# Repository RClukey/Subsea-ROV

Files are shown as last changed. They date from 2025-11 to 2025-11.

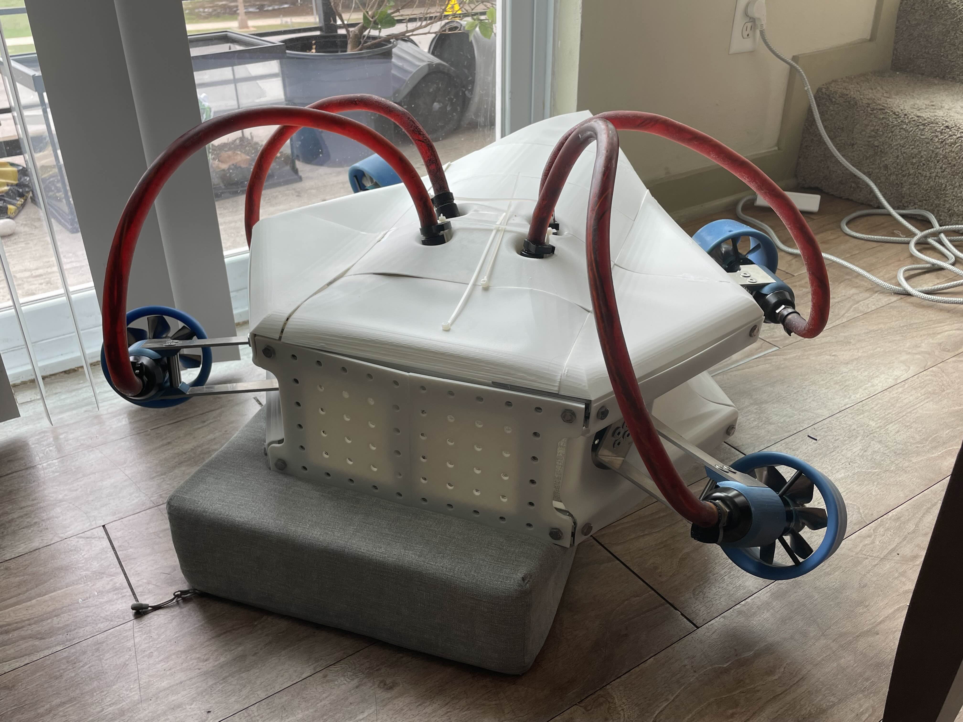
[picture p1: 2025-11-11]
Images-Videos/ROV Model Left.jpg

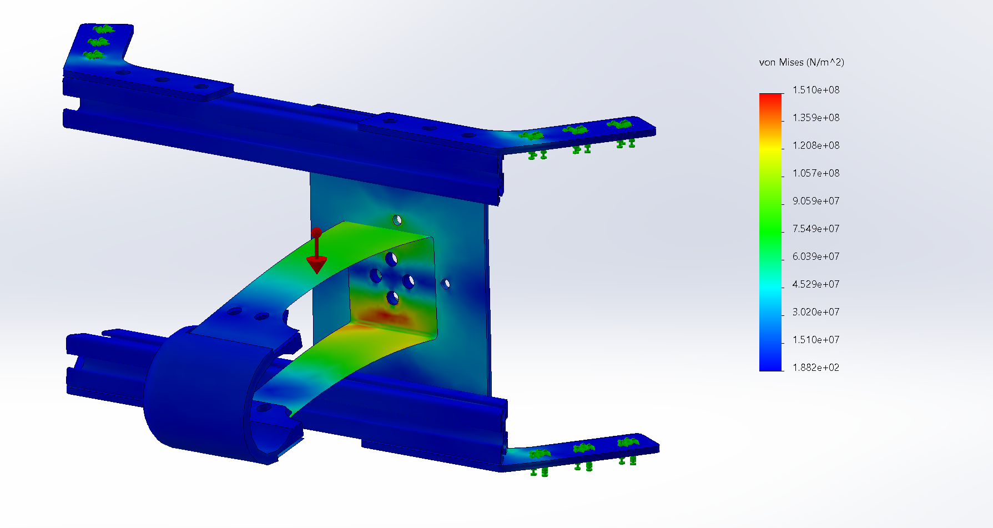
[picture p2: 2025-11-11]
Images-Videos/ROV Force Impact Simulation.png

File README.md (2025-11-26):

# Subsea Remotely Operated Vehicle (ROV)

During my robotics capstone at Texas A&M, my team and I were tasked to develop a subsea remotely operated vehicle (ROV). I led the CAD design and simulation work using SolidWorks, using the equations tool in SolidWorks to rapidly redesign the product based on the evolving client specifications. Each iteration of the design was simulated using SolidWorks' finite element analysis and hydrodynamics simulations to test the model's structural integrity and performance underwater. Once the core of the ROV's design was finalized, the team transitioned to fabricating the prototype to physically simulate the design in the real world. Even then, we continued making daily adjustments to the design improving strength, buoyancy, and hydrodynamics, which meant the physical model had to be altered to match the newer SolidWorks designs. Working in that rapidly iterative environment — constantly shifting between digital modeling and hands-on validation — taught me how to move quickly, troubleshoot effectively, and stay adaptable to the specifications of the design.

The CAD Models repository includes all the CAD models that were used to create the design for the ROV structure and propulsion system.

The Images-Videos repository includes a lot of the pictures and videos throughout the project.

SubseaROV_DOF-Animation.gif shows the CAD design and range of motion of the thrusters for the subsea ROV. Each thruster has independent rotation controls and thrust controls allowing for full 6 degrees of freedom.

SubseaROV_Mid-Report.pdf shows the mid-semester report for our capstone team, after the design was determined, but before the design was fabricated.

SubseaROV_Final-Report.pdf shows the end of semester report for our capstone team, after the design was fabricated and tested.

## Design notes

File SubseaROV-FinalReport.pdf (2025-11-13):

## Final Design Report Next-Generation Subsea ROV

## Prepared For: Mr. William Ledbetter Mr. Don Wells

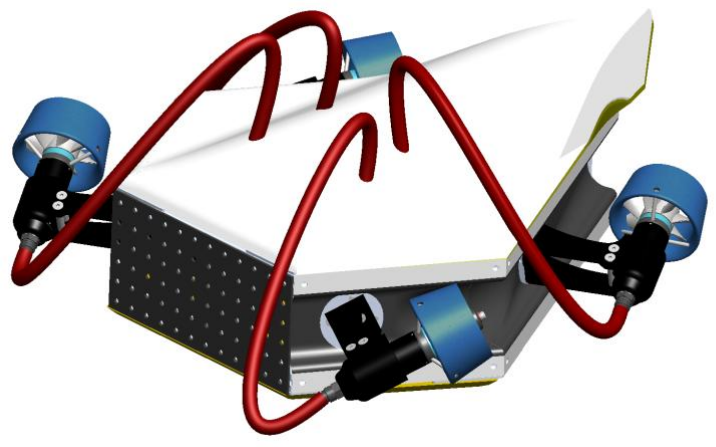
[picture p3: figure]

## Presented to Dr. Andrew Conkey

## Prepared by: Ocean Gig Eric Bauman Bobby Clukey Heath Garrett Marcus Navas David Scott

## Texas A&M University Department of Multidisciplinary Engineering ITDE 402 – Spring 2025 – Sections 501/M01

## April 21, 2025

Texas A&M University-MTDE-Final Report. – Ocean Gig | 2

Executive Summary
Next-Generation Subsea ROV

When divers operate underwater, they encounter numerous hazards inherent to the environment. To reduce these risks, underwater remotely operated vehicles (ROVs) have been developed to minimize the need for direct human involvement in dangerous conditions. However, current ROVs lack the ability to move and perceive their surroundings with the same flexibility and precision as a human diver. The objective of this project was to develop an ROV capable of replicating diver-like movement and performing tasks typically executed by divers. The specific focus for this team was the design and construction of the chassis and propulsion systems.

At the start of the semester, preliminary progress had been made in computer-aided design (CAD), and many analytical aspects of the project had been outlined. However, all work up to that point remained theoretical, with no physical components assembled. The only available hardware consisted of thrusters that had been generously donated, as well as the electronics to power these thrusters.

This report presents the analytical diagrams and charts used to identify critical needs, functions, and design solutions that contributed to the development of the final product. It also includes financial documentation to confirm the project remained within budget, along with a detailed overview of the ROV’s construction process.

The completed project resulted in a fully built ROV chassis with thrusters capable of providing six degrees of freedom. This configuration enables the ROV to maneuver through water in a manner that closely simulates the movements of a human diver. With this completed model, the team was able to test the 6-degrees of freedom of the ROV, the strength of the ROV, and attempted to test the force output of the thrusters given different power inputs.

Special recognition is extended to Professor William Ledbetter and Mr. Don Wells for their generous support throughout the project, and to Dr. Andrew Conkey and Professor Oscar Lopez for their assistance throughout the capstone project. Appreciation is also given to members of Oceaneering International, Inc. for their valuable insights and willingness to share their expertise in subsea ROV technology.

Texas A&M University-MTDE-Final Report. – Ocean Gig | 3

Demonstration of ABET Student Outcomes and Performance Indicators

Student Outcome (SO) | Performance Indicator (PI) | Page Numbers in this Report Showing Demonstration of this SO/PI
SO 1: An ability to identify, formulate, and solve complex engineering problems by applying principles of engineering, science, and mathematics | 1-A. An ability to identify complex engineering problems and initiate problem-solution processes | Pages 7-13
| 1-B. An ability to carry out an engineering problem solution process to completion | Pages 24-28
| 1-C. An ability to apply fundamental principles of engineering, science, and mathematics in an engineering problem-solution process | Pages 22-23 Pages 30-32
SO 2: An ability to apply engineering design to produce solutions that meet specified needs with consideration of public health, safety, and welfare, as well as global, cultural, social, environmental, and economic factors | 2-A. An ability to determine needs to be satisfied by an engineered solution and interpret and consider needs in contexts of health, safety, welfare, global, cultural, social, environmental, and/or economic contexts, as appropriate. | Pages 33-35
| 2-B. An ability to implement a logical, orderly, and documented design process driven by defined needs. | Pages 14-21
SO 5: An ability to function effectively and professionally on a team whose members together provide leadership, create a collaborative and inclusive environment, establish goals, plan tasks, and meet objectives | 5-A. An ability to function effectively on a team by contributing to the team effort through collaboration and the creation of a collaborative and inclusive environment. | Pages 38-40
| 5-B. An ability to function effectively on a team by exercising appropriate leadership to establish goals, plan tasks, and meet objectives. | Pages 7-8 Pages 38-40
SO 6: An ability to develop and conduct appropriate experimentation, analyze and interpret data, and use engineering judgment to draw conclusions and propose recommendations | 6-A. An ability to develop and conduct experiments appropriate for engineering applications. | Pages 22-23 Pages 30-32
| 6-B. An ability to analyze and interpret experimentally derived data. | Pages 22-23 Pages 30-32
| 6-C. An ability to use appropriate engineering judgment with analysis of experiments to formulate conclusions and propose recommendations. | Pages 22-23 Pages 30-34

Texas A&M University-MTDE-Final Report. – Ocean Gig | 4

## Final Design Report

Next-Generation Subsea ROV

### Table of Contents

EXECUTIVE SUMMARY | 2
DEMONSTRATION OF ABET STUDENT OUTCOMES AND PERFORMANCE INDICATORS | 3
List of Figures and Tables | 5
Glossary/Nomenclature | 6
INTRODUCTION | 1
Project Recap | 1
Concept Overview | 3
Initial Concept | 3
Modified Concept | 5
DETAILED DESIGN OVERALL SYSTEM | 8
Functional Diagrams | 8
Functional Analysis Diagrams (FAD)/Functional Flow Diagram (FFD) | 8
Physical Layout Diagrams | 9
Geometric Layout | 11
Bill of Materials | 13
Estimated Cost for Prototype | 15
DETAILED DESIGN: ENGINEERING ANALYSIS | 16
“THE BUILD” -FABRICATION/CONSTRUCTION/PRODUCTION/SYNTHESIS/CODING | 18
Stage 1: Frame Construction | 18
Stage 2: Thruster Arm Construction | 19
Stage 3: Skin Construction | 21
Stage 4: Electrical Connection | 23
Testing/Verifying/Validating/Experimental Plan | 24
Safety/Hazard Assessment and Evaluation | 27
RELIABILITY ASSESSMENT | 28
SOCIETAL FACTORS AND IMPACT | 29
FUTURE WORK | 30
TEAM AND PROJECT ORGANIZATION, PLANNING, AND EXECUTION | 32
SUMMARY | 35
Appendix | 36
A. List of Abbreviations and Terminology | 36
B. References | 36
C. Order of Magnitude and Detailed Calculations | 37
E. Detailed working drawings/models/assembly | 38
F. Testing/Validating/Verification/Experimentation | 39

### List of Figures and Tables

Figure 1. Chassis Subsystem House of Quality (team-fig) - 1 Figure 2. Propulsion Subsystem House of Quality (team-fig) - 2 Figure 3. Isometric drawing of The Turkey design. (team-fig) - 3
Figure 4. The final fall semester CAD drawing (team-fig) - 4
Figure 5. The mid-semester model of the ROV (team-fig) - 6
Figure 6. The final design of the ROV without the syntactic foam (team-fig) - 7 Figure 7. The final design of the ROV with the syntactic foam (team-fig) - 7
Figure 8. Functional Analysis Diagram for the subsea ROV. (team-fig) - 9
Figure 9. Physical layout of the chassis and propulsion subsystems (team-fig) - 10
Figure 10. Wiring diagram for the thruster power and control system provided by Tecnadyne. (Tecnadyne)
- 10
Figure 11. Internal view of the ROV showing the electronics, syntactic foam, frame, rotary actuators, and thruster. (team-fig) - 11
Figure 12. Exploded view of the ROV showing the key components of this phase of the design project. (team-fig) - 12
Figure 13. Calculations of Archimedes’ Principle in SolidWorks. (team-fig) - 16
Figure 14. A team member cuts an aluminum bar using an FEDC chop saw. (team-fig) - 18
Figure 15. The completed aluminum frame of the chassis. (team-fig) - 19
Figure 16. A team member prepares to bend the aluminum section of the thruster arms. (team-fig) -20 Figure 17. A thruster sitting in the thruster clamp and aluminum arm. (team-fig) - 20
Figure 18. Top skin panel with space for the clips on the thruster tubing. (team-fig) - 21
Figure 19. Port isometric view of the ROV with the skin panels (team-fig) - 22
Figure 20. Starboard isometric view of the ROV with the skin panels (team-fig) - 22
Figure 21. The wiring for the power subsystem is connected to the subsea thruster. (team-fig) - 23 Figure 22. Stress/strain curve for 5052 Aluminum (team-fig) - 24
Figure 23. Stress heat map for a 50-pound force acting on the thruster clamp acting downward with the thruster arm horizontal (team-fig) - 25
Figure 24. Stress heat map for a 90-pound force acting on the thruster clamp acting downward with the thruster arm vertical (team-fig) - 26
Figure 25. The WBS for the design and manufacturing process. (team-fig) - 33
Figure 26. The projected Gantt chart for the semester. (team-fig) - 33
Figure 27. The actual completion times for tasks are between March and April. (team-fig) - 34

Figure C.1. Calculations of Archimedes’ Principle in SolidWorks. (team-fig) - 37
Figure C.2. Excel representation of the resultant force and torque vectors given thruster positions and output forces. (team-fig) - 37
Figure E.1. Enlarged model of the wiring diagram for the thruster power and control system - 38 Figure F.1. Enlarged representation of the resultant force and torque vectors given thruster positions and output forces. (team-fig) - 39

Table 1. SWOT Analysis for the ROV (team-fig) - 5
Table 2. Bill of materials for the prototype (team-fig) - 13-14
Table 3. Cost estimate table for the project (team-fig) - 15
Table 4. Future work areas that will be covered in coming years (team-fig) - 30-31

Texas A&M University-MTDE-Final Report. – Ocean Gig | 6

### Glossary/Nomenclature

- CNC: Computer Numerical Control
- DOF: Degrees Of Freedom
- FAD: Function analysis diagram
- Full Depth Rated: Rated to withstand the pressures at the bottom of the Marianas Trench, the deepest part of the ocean.
- Propwash: The effect that thrusters have on the fluids passing through them. This effect makes the fluids rotate in a spiral pattern after passing through the propeller.
- ROV: Remotely Operated Vehicle
- SWOT: Strengths, Weaknesses, Opportunities, and Threats
- Tether (Umbilical): The wired connection between the ROV and the pilot on the surface which powers the ROV and controls the thruster directions and powers.
- WBS: Work Breakdown Structure

Detailed Design Report-FR– | Spring 2025

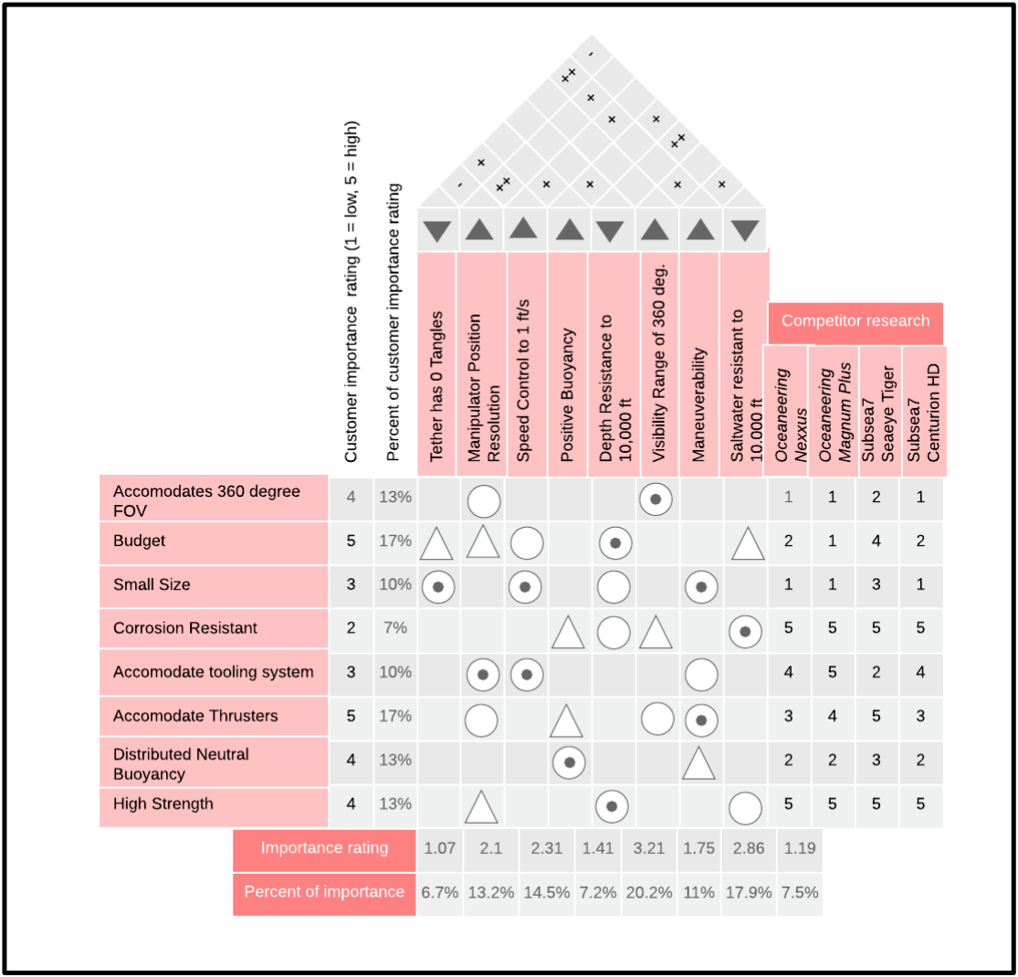
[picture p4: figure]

Texas A&M University MTDE– Ocean Gig | Page 1

Introduction

Project Recap
The goal of this project is to create a Subsea ROV that possesses the ability to move and see like a human diver. This constitutes characteristics such as the ROV having 6 degrees of freedom, access to 360 degrees of visibility, and having a borescope to be able to look around objects the way a human head/neck combination provides. From the QFDs (Figures 1 and 2 ), the team determined the top-level measures that produce a successful project, including keeping the overall cost of the ROV minimal within the team's budget and keeping the maneuverability of the ROV ahead of the current industry leaders in subsea ROV about tether accommodation and thruster capability.

Figure 1. Chassis Subsystem House of Quality (team-fig)

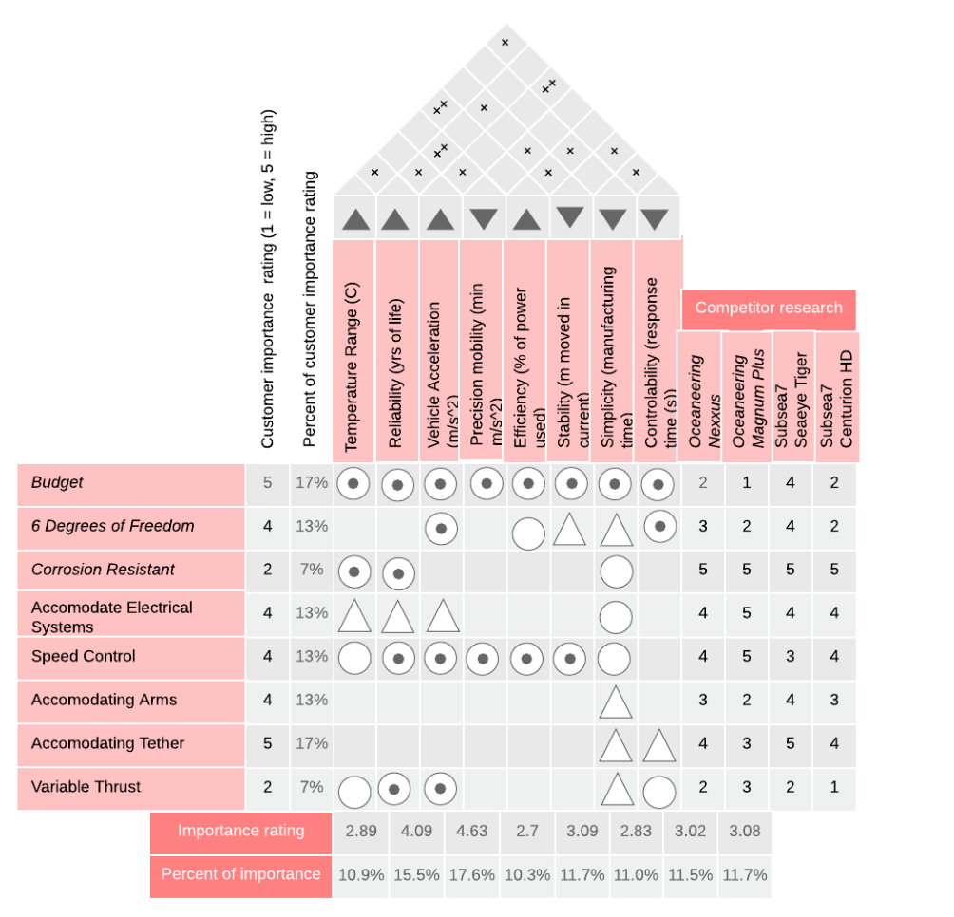
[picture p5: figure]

Figure 2. Propulsion Subsystem House of Quality (team-fig)

As the design progressed, the focus shifted to the more fundamental deliverables. A well-designed frame that provided efficient use of space to accommodate electronics, a buoyancy system, and the rotating thrusters were paramount. We also put a deeper focus on completing the mounting of the thrusters to be able to represent our proof of concept within the time frame we were working within. We kept the needs of the QFD in mind by prioritizing the design of the frame conscious of buoyancy, as that is the determining factor in an ROV that functions under the water, as well as making sure the thrusters can provide the control that is key to our project.

Concept Overview
This section of the report covers the development of the initial solution to the need statement and how that concept evolved to the final design the team worked towards.

Initial Concept

At the beginning of the semester, the dimensions of the frame had been essentially finalized, having decided on an optimum shape. The mounting location of the thrusters and rotary actuators was also known. The rotary actuators would not be implemented into the final design due to the heavy power needs, weight, and expensive cost. The skin panel shapes were also roughly determined based on the desire to create a hydrodynamic shape that provided strength as well as thruster, tether, manipulator, and camera accommodation.

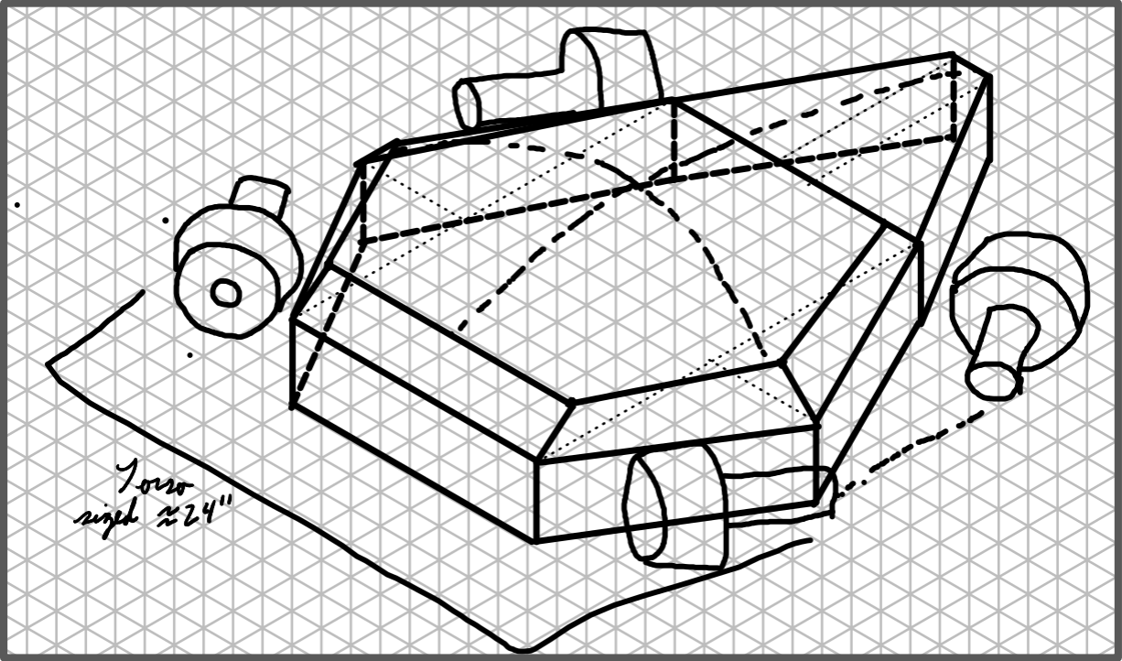
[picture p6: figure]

Figure 3. Isometric drawing of The Turkey design. The design was planned to be 24 inches long, 25 inches wide, and 10 inches tall. These dimensions are consistent with the prototype. (team-fig)

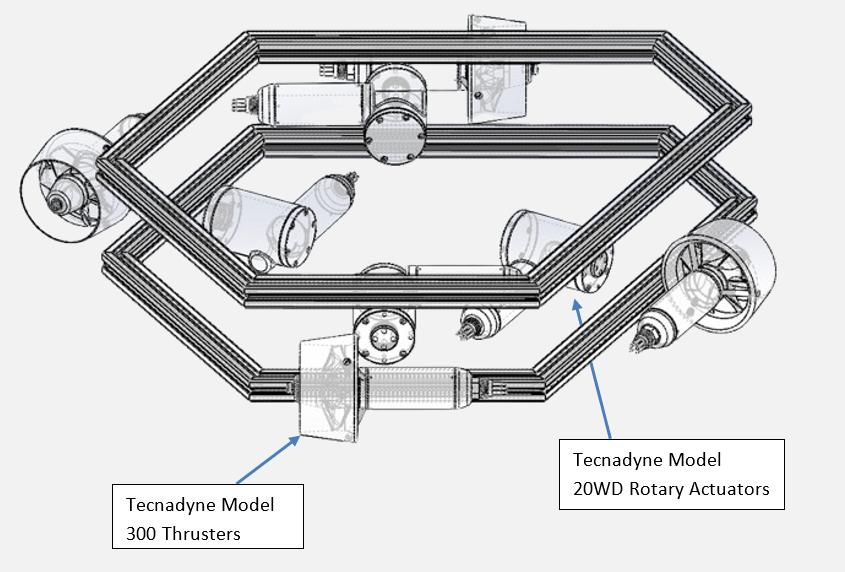
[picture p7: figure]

Figure 4. The final fall semester CAD drawing with the Tecnadyne Model 300 thrusters and Tecnadyne Model 20WD rotary actuators labeled. (team-fig)

Most of the strengths of the ROV project came from this being a multi-year project. As this was the third year of a five-year project, the team had two years of work to build upon. One of the strengths that didn’t come from the length of the project was the modularity and scalability of the design of the ROV. If the dimensions of the beams and the power of the thrusters were to be increased, the capabilities of the ROV, such as the payload and depth resistance, could also be increased.

The weaknesses of this project stemmed from the lack of experience the team had with certain parts of the project’s scope. Part of our work was to create the power system for the ROV. None of the team members in the project were power engineers, and as such, no one had experience working with the power system. Another weakness came from the project’s budget. The rotary actuators the team was going to use cost $12,000 each. This means the 4 rotary actuators that had originally been planned for would go well over the budget of $10,000.

The opportunities that this project has given the team come from the design of the ROV and the industry leaders who have been able to help with the creation of the ROV. The 6 degrees of freedom on the ROV provide multi-directional capabilities that mimic a diver’s motions. The team also worked with Oceaneering and The Subsea Tieback Foundation to determine how the current industry creates subsea ROVs and where the current solutions could be improved upon to create the next-gen ROV design.

The threats to the ROV project, much like the weaknesses, came from the lack of knowledge in power engineering. None of the team members were power engineers, and as such, the team needed to learn how to deliver the necessary power to the thrusters, rotary actuators, cameras, and manipulators for the ROV to function like a human diver. Another threat to the project, which can be a major problem in future stages of the project, is that the team’s sponsors specifically stated that marinization should not be a priority. This could affect how much of the team's work will be useful to the future years of the project. Something the team might have thought was important to design the ROV around might not be marinized, and as such would have to be replaced, thus changing the design of the project.

Table 1. SWOT Analysis for the ROV (team-fig)

Strengths: ● Concept ● Industry connections through sponsors ● Static Mechanical analysis ● Access to previously acquired parts ● Access to previous work done ● Modularity and scalability of design | Weakness: ● Undeveloped power system ● Lack of full CAD model ● Vagueness of certain specifications ● Lack of access to CAD models for electrical components ● Potential costs ● Fluid analysis ● Limited testing environment
Opportunities: ● Advanced Maneuverability ● Size-accommodated exploration possibility ● Innovation in overall geometry ● Creation of a next-gen ROV that mimics the motions of a human diver ● Modularity and scalability of design ● 6 degrees of freedom | Threats/Risks: ● Needing expensive parts and possibly going over budget for specific pieces of equipment ● Understanding of circuitry for power systems ● Our part of the project is not concerned with marinization, which could cause compatibility issues further down the road ● Combining previous groups' work into our frame

Modified Concept

The main shape of the ROV remained constant throughout the semester, however the externals of the ROV went through various changes to best shape for hydrodynamics, buoyancy, and overall ROV strength.

In the beginning of the semester, there was only the frame, thrusters, and rotary actuators in the ROV model. The dry weight for this version of the ROV was 46.2 pounds, while the wet weight was 32 pounds.

The first modification to the design of the ROV included adding the syntactic foam used for floatation and close to neutral buoyancy and the electronics that would power the thrusters. However, no skin was included to protect the internals of the ROV. The majority of the syntactic foam was positioned above the ROV to raise the center of buoyancy, the geometric center of the ROV, above the center of mass. This will allow the ROV to orient itself right-side up. The closer the center of mass and center of buoyancy were together, the slower the ROV would self-orient, meaning less force would be required from the thrusters to maintain an angled position if the ROV requires an angle while in operation. The dry weight for this version of the ROV was 71 pounds, while the wet weight was 3.3 pounds. This was a significant improvement from the initial design of the ROV. The team chose not to aim for true neutral buoyancy, as the addition of the manipulator to the front of the ROV would affect the ROV’s center of mass and the overall buoyancy.

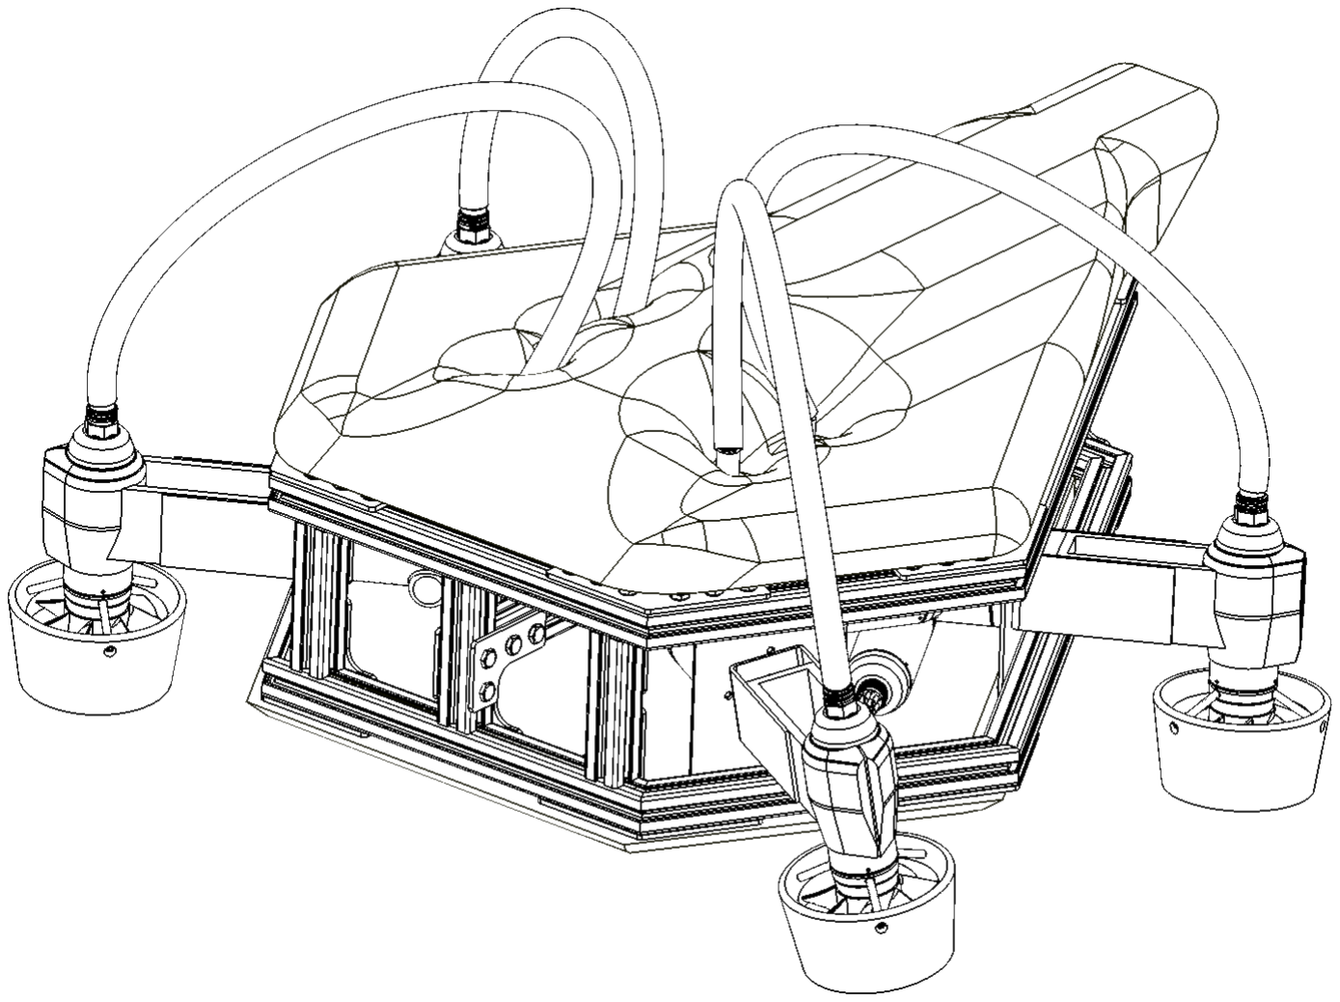
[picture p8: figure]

Figure 5. The mid-semester model of the ROV (team-fig)

The next and final improvement on the design came with the skin panels on the sides, top, and bottom. The skin panels protected the important electrical components inside the ROV and the syntactic foam from being damaged. The panels also prevented fish and other sea creatures from getting inside the ROV and affecting the operations of the ROV. The panels also provided a rigid body for water to flow around, instead of having the turbulent water from the thruster flow through the ROV, thus improving the hydrodynamics of the ROV. This design also came with a slight modification to the design of the syntactic foam because the introduction of the skin panels and an atmospheric pressurized vessel for the electronics affected the wet weight of the ROV. The dry weight for this final version of the ROV was 72.4 pounds, while the wet weight was 2.9 pounds. The skins on the side of the ROV allowed for optimal flow of water through the thrusters while decreasing the effects of propwash between the thrusters and providing protection to the electronics and syntactic foam to prevent damage.

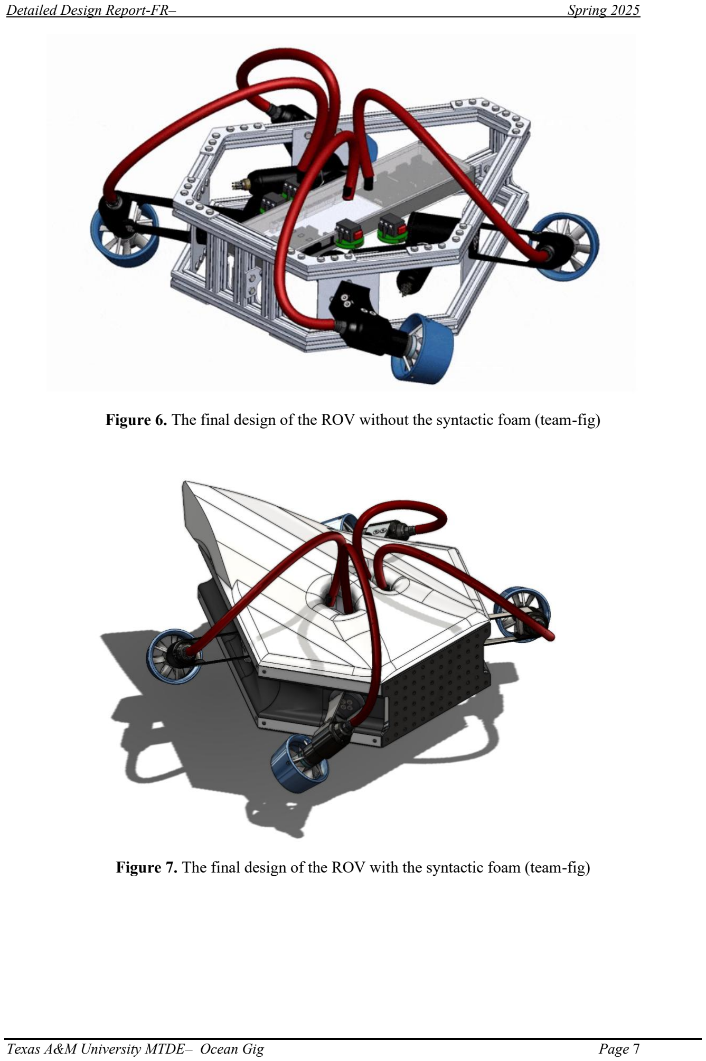
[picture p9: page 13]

Figure 6. The final design of the ROV without the syntactic foam (team-fig)

Figure 7. The final design of the ROV with the syntactic foam (team-fig)

Detailed Design Overall System
This section details the chain of interfacing design elements that will result in a product that completes defined function requirements. These tools lay out the path of travel from power and/or operator input to output by the design prototype. This is an opportune way to understand how the product was designed and what components are responsible for intermediate functions, multiple functions, and how key design requirements had to be revised since brainstorming and proof of concept. This is a relevant mindset for this project in particular as this stage of the ROV design contained chassis and propulsion system design aspects.

This next-generation ROV’s unique thruster capability and optimized shape is shown through detailed design diagrams to have important relationships, while still maintaining numerous independent design elements. For example, the functional flow diagram shows that the camera system will relay information through the electronics and allow the operator to take advantage of the more convenient chassis shape and thruster-provided degrees of freedom.

Functional Diagrams
These diagrams display the functional “path” of the design. Via the design requirements, projects are designed with the end operations in mind, and by understanding the components involved and how they interact with one another, a sort of roadmap can be created to flow through the interfaces from inputs to outputs, with outputs being the aforementioned design requirements. In the case of the ROV, this will mainly pertain to the mobility of the ROV being provided through the thrusters via electrical power, with the chassis holding everything steady.

Functional Analysis Diagrams (FAD)/Functional Flow Diagram (FFD)

The functional analysis diagram is the roadmap from operator inputs to ROV motion and vision. This diagram outlines the ROV’s design capabilities from the point that the operator inputs a command based on their senses via the cameras that will be integrated into the ROV. This operator input is transmitted to the ROV’s electronic systems via the tether. The electronic systems control the cameras, rotary actuators, manipulators, and thrusters, which will allow these subsystems to function as intended. The chassis provides structural support and protection for these components by being designed such that the frame takes the force of the impacts, and the skin prevents rocks and fish from damaging the electronics. The thrusters provide movement to the ROV via the propellers, however, the water can also move the ROV through currents that must be taken into account.

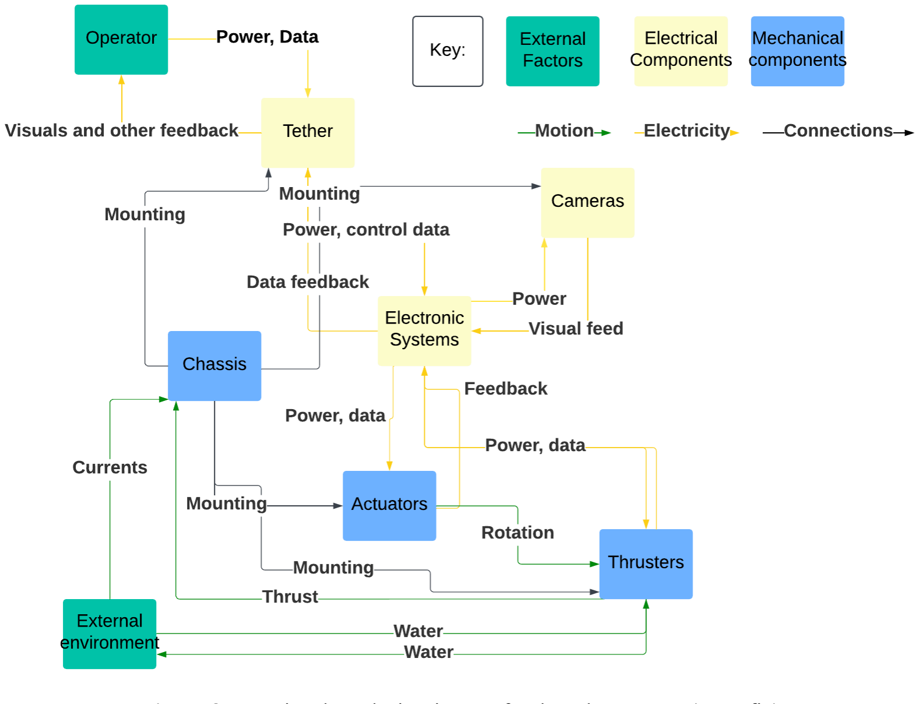
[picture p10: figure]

Figure 8. Functional Analysis Diagram for the subsea ROV. (team-fig)

Physical Layout Diagrams

Chassis and propulsion layout:

The chassis and propulsion layout is shown below in Figure 9 & 10. This shows the locations of the syntactic foam, electronics, frame, rotary actuators, thrusters, and skin about each other. The syntactic foam is on both the bottom and top to provide buoyancy to the ROV. The electronics are encased in an atmospheric pressure vessel full of air so the electronics can function underwater. The frame is constructed out of aluminum bars and sheet metal, and stainless steel bolts and fasteners. The rotary actuators and thrusters come from Tecnadyne, both of which are full-depth rated (11,000 meters). Lastly, the skin is made out of ABS plastic which would be vacuum-formed using molds to protect the ROV.

## Skin

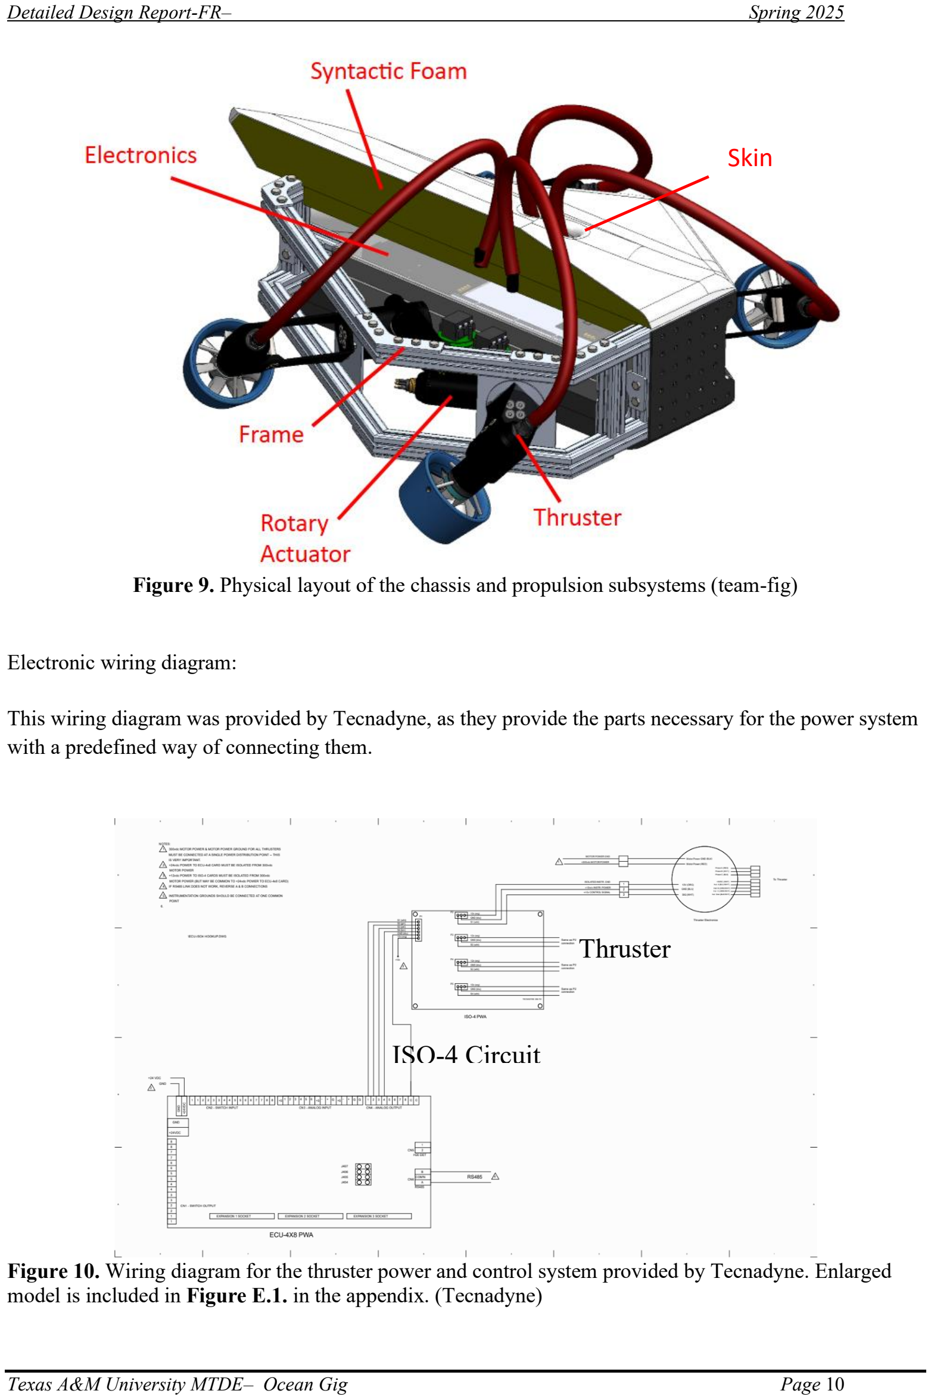
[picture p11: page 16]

Figure 9. Physical layout of the chassis and propulsion subsystems (team-fig)

Electronic wiring diagram:

This wiring diagram was provided by Tecnadyne, as they provide the parts necessary for the power system with a predefined way of connecting them.

Figure 10. Wiring diagram for the thruster power and control system provided by Tecnadyne. Enlarged model is included in Figure E.1. in the appendix. (Tecnadyne)

## Thruster

## ISO-4 Circuit

The power subsystem, excluding components that only are used to affect the control voltage, properly begins at the ISO-4 card and continues to the thruster electronics module and into the thruster itself (not shown).

The ISO-4 circuit boards take in a 12V DC instrumentation power signal and four +/- 5V control signals, and outputs four isolated sets of 12V instrumentation power and a +/- 5V control signal. These signals are what is passed into the thruster electronics module and from there into the thruster.

The thruster electronics module takes in the signals from the ISO-4 circuit board as well as a separate, isolated 300V power source, conditions these signals, and passes them to the thruster.

The separate circuit board that is not part of the power system is an ECU 4x8 BIOS, which takes in computer commands and outputs a corresponding control signal voltage between -5 and +5 volts.

Geometric Layout

The Subsea ROV capstone project for the 2024-2025 school year consisted of chassis and propulsion design engineering. The geometric layout will provide diagrams and point out the key components of said chassis and propulsion components that were designed to meet the client's specifications for the next-generation ROV design prompt. Provided are cutaway views as well as exploded models to better understand the ROV and the interfacing of the components, as this is a key part of the 2 overarching design areas. The chassis was designed with the intention of providing a diver-like shape that will be noticeable in use, but also to receive the thruster system that will constitute the execution of free movement in all 6 degrees of freedom as one would be capable of doing were they underwater.

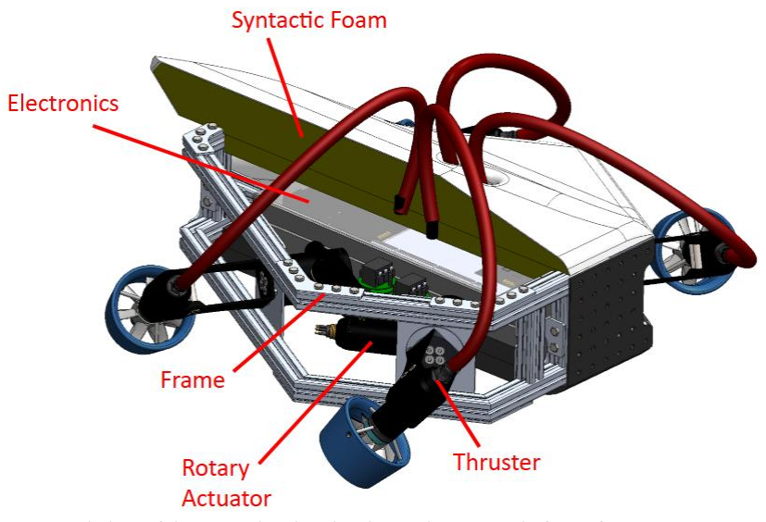
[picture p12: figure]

Figure 11. Internal view of the ROV showing the electronics, syntactic foam, frame, rotary actuators, and thruster. (team-fig)

Figure 12. Exploded view of the ROV showing the key components of this phase of the design project. (team-fig)

The ROV model displayed above is the final iteration of the design. The ability to see the final shape of the constructed prototype as well as the inside of the top and side skin panels connects the dots between the overall shape and components. The skin gives way to the frame, designed with the previous team’s coffin shape in mind but now optimized to provide structural rigidity and be easily scalable to accommodate the growing amount of centrally-placed electronic components that will power systems in the future. The frame is intended to provide a hydrodynamically advantageous shape of a human torso when submerged, emphasized by the smooth, curvaceous skin panels. The inside of the ROV is available to future teams for power components, control system electronics such as rotary actuators, and the syntactic foam that will be calibrated to provide near-neutral buoyancy. The thrusters are placed between the angled sections of the frame on the port and starboard faces. This placement is strategic to the 6 degree of freedom design goal. The free rotation that will be provided by the rotary actuators will allow for the thrusters’ angles of orientation to allow a force vector in any direction, allowing the operator to move freely without limitation or the necessity of calculating every adjustment based on the limited mobility of the ROV.

Bill of Materials

Table 2. Bill of materials for the prototype (team-fig)

Item No. | Sub System description | Part Specs | Description | Cost Per Unit | Quantity | Total Cost
1 | Extruded Aluminum Bars | 1”x3’, solid, smooth finish | Aluminum bars serve as light but rigid frame sections. Extruded quality will allow for effective component mounting and allow adjustments. | $15.90 | 7 | $110
2 | Sheet Aluminum 5052 | 1/8”, 24” x 24” | One sheet of specified grade aluminum; is used to supply frame connecting brackets, as well as thruster mounting hardware. | $99.06 | 1 | $100
3 | Stainless Steel Extrusion Nuts | 1/4”-20 | Specialized fasteners to accommodate the extruded aluminum frame. | $9.13 per 10 | 15 | $137
4 | 316 Stainless Steel Hex Head Screw | 1/4”-20, 3/8” | The screws that will be used to fasten the frame sections and brackets together. Specific sizes were needed to accommodate the gap in the aluminum bars and the thread specifications of the nuts. | $5.38 per 25 | 6 | $32
5 | 316 Stainless Steel Hex Head Screw | 10-32, 3/4” | These screws are used to fasten frame components and thruster mounting hardware together and to the frame. | $4.80 per 10 | 2 | $10
6 | 316 Stainless Steel Hex Head Screw | 1/4”-28, 3/4”, 82° countersink | The countersink screws are used to secure the rotating thruster mounting brackets to the vertical plates attached to the frame. There are 4 per thruster. | $3.84 per 5 | 7 | $27
7 | 316 Stainless Steel Round Coupling Nut | 1/4”-28, 1-1/4” | The coupling nuts are hollow cylindrical threaded fasteners to be placed between the bent plates of the thruster mounting arms and the printed thruster clamp to create the clamping force upon the thrusters | $10.97 | 8 | $90
8 | ABS Sheet | 36" x 36" x 1/16" | This sheet of basic plastic will be used to form the preliminary skin model shape | $35.71 | 4 | $145

9 | Tecnadyne Model 300 Thrusters | 475W 17 lbf forward thrust / 7 lbf reverse thrust 2.8-3.1 lbs or 1.8-2.8 lbs (submerged) depending on the configuration 2,800ft (850m) depth rating | Thrusters capable of providing forward and reverse thrust at the desired quantity to move the ROV with precision and efficiency without being difficult to control. Capable of running at various voltage levels and with adjustable analog speed. The thrusters are rated at appropriate depths of current industry offshore rigging. The thrusters are generously donated by sponsors but are mounted without power to the ROV due to difficulty acquiring a sufficient source to power them. | $7,500 | 4 | $30,000
10 | Tecnadyne Model 20W Rotary Actuators | 150-300W Output speeds of 1.5 RPM to 45 RPM 20 ft-lb of tq 2.5-5 lbs or 1.6-3.2 lbs (submerged) depending on the configuration Full depth rated | Rotary actuators are intended to provide the amount of force and responsiveness to orient the thrusters as we imagined. Variable output speed and adjustable analog speed allow for good useability. Lightweight and with depth rating as a non-issue, the actuators will be a key component in the ROV’s functionality. Due to the heavy expense, physical ones are not present in the prototype. | $12,500 | 4 | $50,000
11 | Insta360 X3 CINSAAQ | 360 degree 5.7k footage lightly waterproofed Active HDR Flowstate stabilization | The cameras that will be used in the 360-degree vision capabilities that the ROV is intended to provide. Advanced stabilization and HDR features will render more precise imaging. They will be mounted around the ROV and interfaced with each other as well as a VR headset that will allow the operator to work as if their head is where the ROV is. This model is not a definitive choice, as they are not fully waterproof. | $329.99 | 3 | $990
| | | | | Total | $81,640

Estimated Cost for Prototype

The estimated cost for the prototype was calculated by referencing the cost of parts already purchased, and the estimated cost of parts quoted and unobtained. The off-the-shelf parts include all parts, such as the fasteners, screws, ABS and aluminum sheets, aluminum bars, and 360-degree cameras, ordered by this team and the previous teams, as well as all donated parts. The 3D-printed parts were used for the modeled skin panels and thruster clamps. There was no off-campus production used in the production of the ROV. The TBD expenses include the rotary actuators, syntactic foam, and an estimate for the expense of the following years. Lastly, the consulting expenses come from the cost to Oceaneering International for their consultation with the team, as well as other consults with the FEDC and the Zachar Common Labs.

Table 3. Cost estimate table for the project

Expense Type | Items | Description | Total Cost
Off The Shelf | Fasteners, frame & propulsion system material, skin panel material, thrusters | All the materials were bought to construct the chassis frame, skin panels, and thruster mounting components. The thrusters are available from Tecnadyne to purchase. | $31,426.28
3D Printed | Skin panels, thruster clamps | The clamps that the thruster housing slides into as well as the production of the skin panels using the purchased material | $40
Off-Campus Production | N/A | N/A | N/A
TBD Expenses | General electronics, buoyancy material, systems interfacing, tether accommodation | Any parts of the project phases to come. Primarily the systems integration, controls, and further mechanical engineering necessities. | $65,000
Consulting | Marine and petroleum engineering consulting | Necessary to design a system with awareness of proper marinization and equipment for use around rigging equipment. | $20,000
| | Total | $116,466.28

Detailed Design: Engineering Analysis

During the engineering analysis phase of the design, the team looked at two different

The first use of engineering analysis to the ROV was to determine the ROVs weight in water, or wet weight with syntactic foam. This was an important engineering specification, so the ROV would stay steady in water with little or no force from the thrusters. The goal was to be neutrally buoyant with a tolerance of at most 4 pounds on either side of neutrally buoyant.

Using the detailed CAD model, the overall mass and volume of the ROV was calculated. Using the volume, the team was able to calculate the amount of water displaced by the ROV, which was used to find the buoyant force acting on the ROV. By subtracting the buoyant force from the force of gravity, the team was able to determine the ROVs weight in water. To perform the analysis, the team assumed there were no air pockets in the ROV that were not intentionally put there. In the real ROV, these air pockets would displace more water than was originally counted for, decreasing the ROVs wet weight.

Using the CAD model, the team was able to determine that the dry weight of the ROV was 72.4 pounds and took up a volume of 1,923.5 cubic inches. In sea water, this displaces 69.5 pounds of water. Using Archimedes’ Principle, the ROV design had a wet weight of 2.9 pounds.

Figure 13. Calculations of Archimedes’ Principle in SolidWorks. (team-fig)

This value fits within the team's tolerance of 4 pounds. A weight of 2.9 pounds means the ROV will naturally sink. If power to the ROV is cut, this means the ROV will sink to the ocean floor where it can easily be found and recovered. However, this means all parts on the ROV must be full depth rated, otherwise the ROV could be destroyed if it sinks too deep.

The second use of engineering analysis to the ROV was to analyze the 6-degrees of freedom in the team’s ROV design. This was a very important customer specification as the ROV had to have the characteristics of a human diver.

Each of the four thrusters on the ROV had two variables, the thruster’s rotational position and the thrusters power output, in pound force. Which led to a total of eight independent variables used for finding the overall velocity and rotation of the ROV. For this analysis, the water moving through the thruster was assumed to be laminar. This would not be the case in the real design, but was determined to be a reasonable approximation of the purposes of the engineering analysis. The distances to the center of the clamp holding the thruster were used to calculate the rotational torque vectors that the thrusters would apply to the system. The forces from each thruster were calculated using the rotational position of the thrusters and the geometric shape of the ROV.

Testing the number of degrees of freedom the ROV has was performed in Desmos and Excel by determining the net force and torque vectors given different power and direction inputs to the four thrusters. The Excel spreadsheet was utilized to calculate the resultant force and torque vectors given thruster positions and output forces. Figure F.1. shows the Excel spreadsheet and the resultant forces and torques when all four thrusters are pointing forward and outputting 1 lbf of thrust. As can be seen from the spreadsheet, with all four thrusters pointing forward and outputting 1 lbf of forward thrust, the ROV has no rotational torques, no vertical or lateral forces, and 3.464 pounds of force acting in the longitudinal direction. With a slightly negatively buoyant ROV, 2.9 pounds in water, this provides an acceleration force of 1.2 ft/s^2, excluding the resistance due to water.

“The Build” -Fabrication/Construction/Production/Synthesis/Coding

The build was completed in four primary stages: frame construction, thruster arm construction, skin construction, and electrical connection. Each of these phases had several sub-sections and multiple component parts, often necessitating multiple trips to the FEDC. Each of these phases will be separately discussed and the steps outlined.

Stage 1: Frame Construction

The frame construction was the most complex and labor-intensive part of this build. The first step of this stage was creating the required bars and brackets from the stock aluminum bars and sheets. The brackets were cut out by FEDC staff using a CNC machine, while the aluminum bars were cut to the proper lengths and angles by team members using an FEDC chop saw. The edges of these cuts were then filed for smoothness and safety.

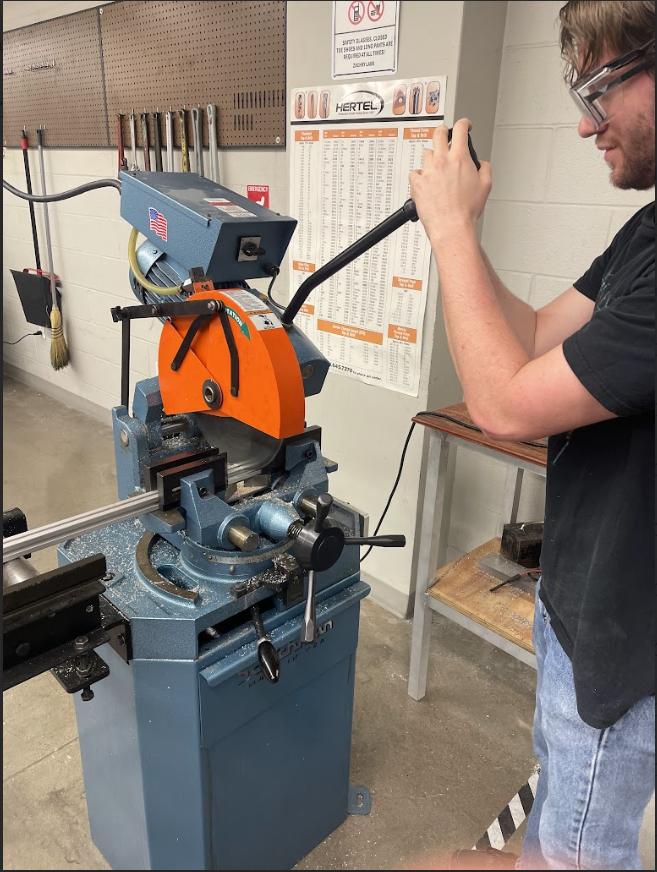
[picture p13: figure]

Figure 14. A team member cuts an aluminum bar using an FEDC chop saw. (team-fig)

After the parts were properly cut out and the fasteners were obtained, the bars and brackets were screwed together. The fasteners were larger than expected, and some of them did not fit in the places they were assigned in the CAD. This tolerance issue was solved by selectively sourcing fasteners that matched the required dimensions in the CAD file. The fasteners that could not be selectively sourced were ground down to ensure their compatibility with the correctly sized fasteners.

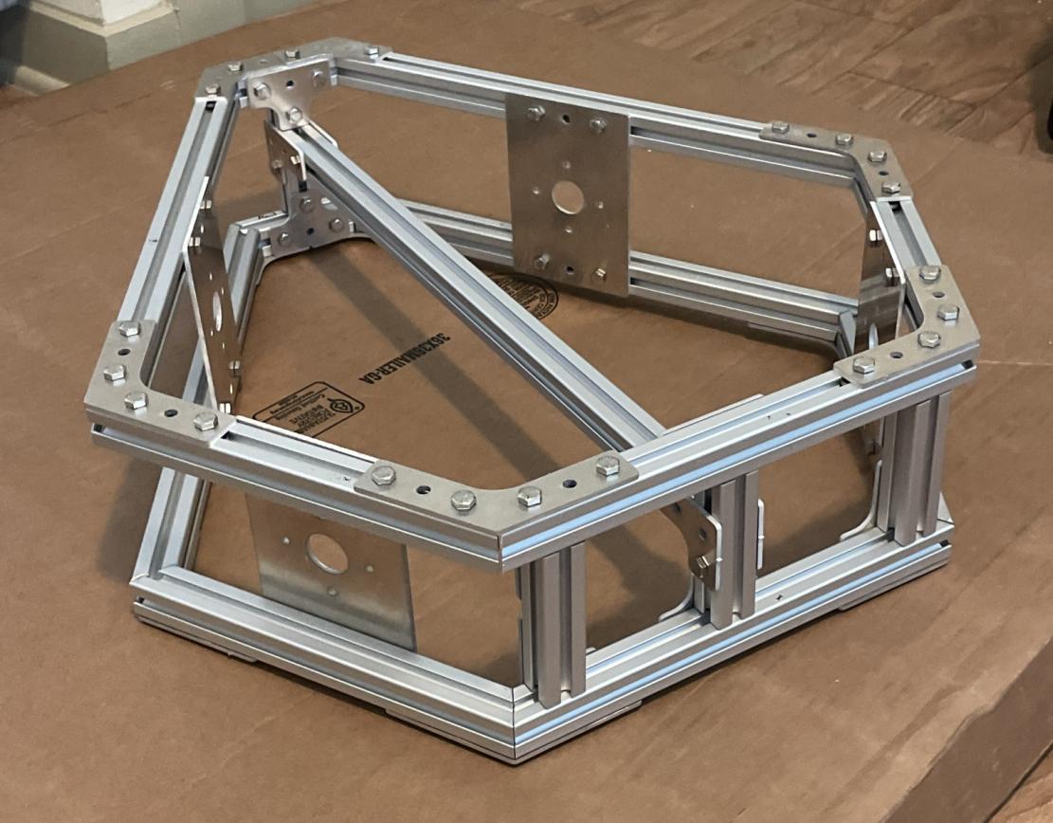
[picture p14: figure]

Figure 15. The completed aluminum frame of the chassis. (team-fig)

Tools used to complete the frame:
- 7/16” hex nut driver - used on the 1/4-20 x 3/8
- 5/16” hex nut driver - used on the 10/32 NF x 3/4
- 5/32” hex key - used on the 1/4-28 NF x 3/4
- Thin stick - used to position the End-Feed T-Slotted Framing Fasteners inside the T-Slotted Frame

Stage 2: Thruster Arm Construction

The thruster arms were constructed from 3 primary parts: an aluminum arm, a 3D-printed thruster clamp, two fasteners, and 3 (parts for allowing rotation). Each aluminum arm was first cut out by FEDC staff using a CNC machine and then bent into the proper shape by a team member at the FEDC. The thruster clamps were 3D-printed using a team member’s 3D printer, as were the (parts for allowing rotation). Each arm was then attached to the aluminum plates on the sides of the frame using additional screws and fasteners.

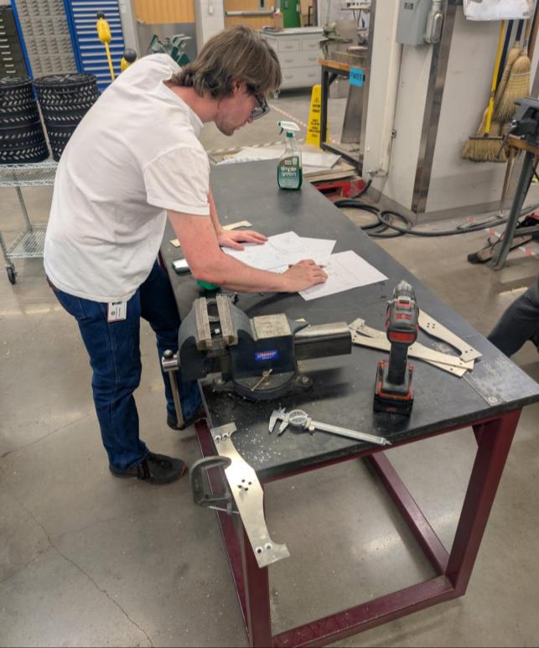
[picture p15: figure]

Figure 16. A team member prepares to bend the aluminum section of the thruster arms. (team-fig)

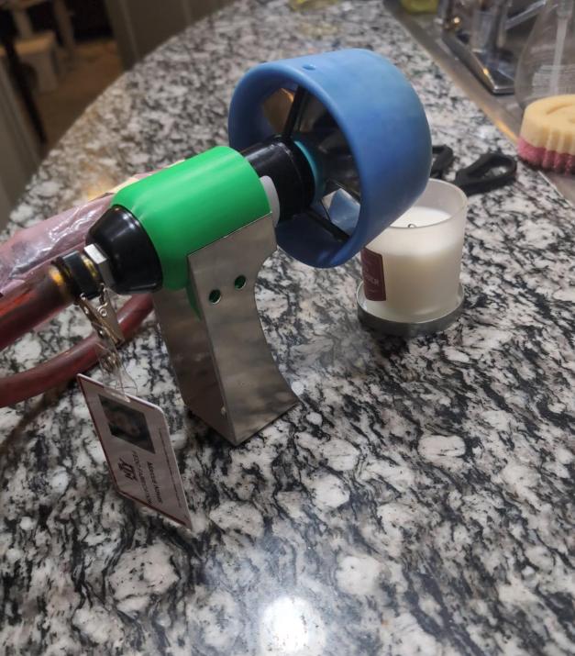
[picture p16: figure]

Figure 17. A thruster sitting in the thruster clamp and aluminum arm. (team-fig)

The clamp model was 3D printed to determine its ease of manufacturability before being manufactured using HDPE. Part of the model was determined to be non-manufacturable and needed to be redesigned.

Stage 3: Skin Construction

All the skin panels were 3D printed. The team wanted to test the overall design of the skin panels on the physical model before forming the real model. The team discovered that a clip on the thruster tube, which hadn’t been accounted for in the CAD model, made the gaps for the tubing too small. This oversight was accounted for in the most recent CAD designs that came after the prototype was fabricated. Figure 18 shows the updated CAD model with space for the clips taken into account.

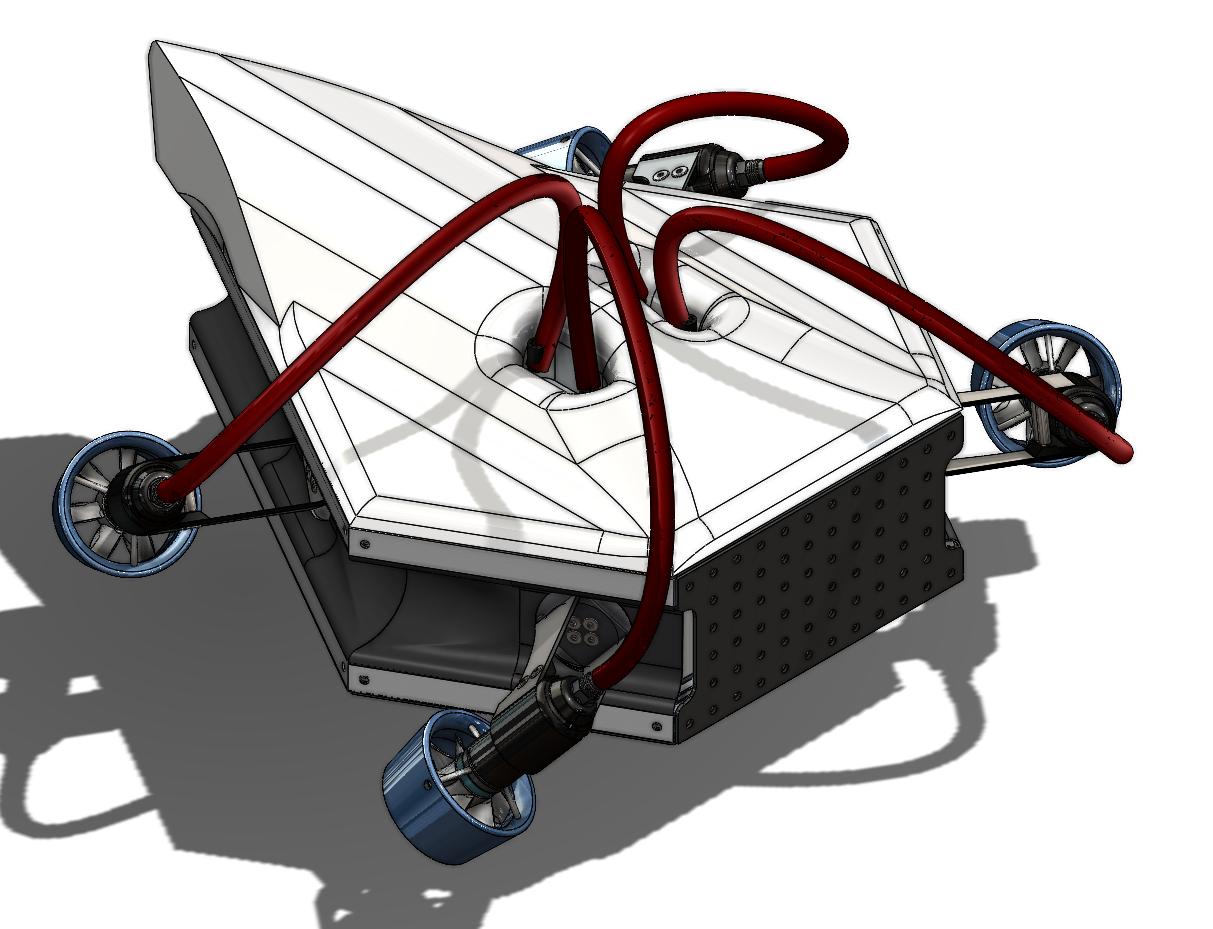
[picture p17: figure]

Figure 18. Top skin panel with space for the clips on the thruster tubing. (team-fig)

The side skin panels covering the front two thrusters were small enough to print as one piece, however, every other skin panel needed to be split into multiple pieces to fit in the 3D printer, requiring them to be glued together. The team obtained ABS plastic which the following team can use to create the final skin panels. The ABS plastic will be vacuum-formed using molds to shape the skin once the final design of the ROV has been determined by the following capstone teams.

There is no bottom skin panel in the prototype unlike in the CAD because, without the syntactic foam, the 3D-printed material would not be strong enough to hold up the ROV.

Figure 19. Port isometric view of the ROV with the skin panels (team-fig)

Figure 20. Starboard isometric view of the ROV with the skin panels (team-fig)

Stage 4: Electrical Connection

The electrical connections were assembled in parallel and separately from the frame and chassis build. The build was conducted using the information in figure (#) provided by Tecnadyne. The actual build started from the ISO-4 card and connected it to one thruster electronics module and from there to the thruster itself. Some parts, like the ISO-4 card and the motor sensor connector, had standard connections that available wires could be attached to, while some connections required other techniques. Wires were looped around the pins for the control signal and soldered to the wires coming off the ISO-4 card, while the pins connected to the motor power section accepted a wire in between their halves. The cable attached to the thruster was the correct size for standard wires and solder to be connected. However, while the connections into the thruster would properly be soldered in the final product, they were not in this build since the thruster needed to be easily disconnected for verification of the function of the thruster arms.

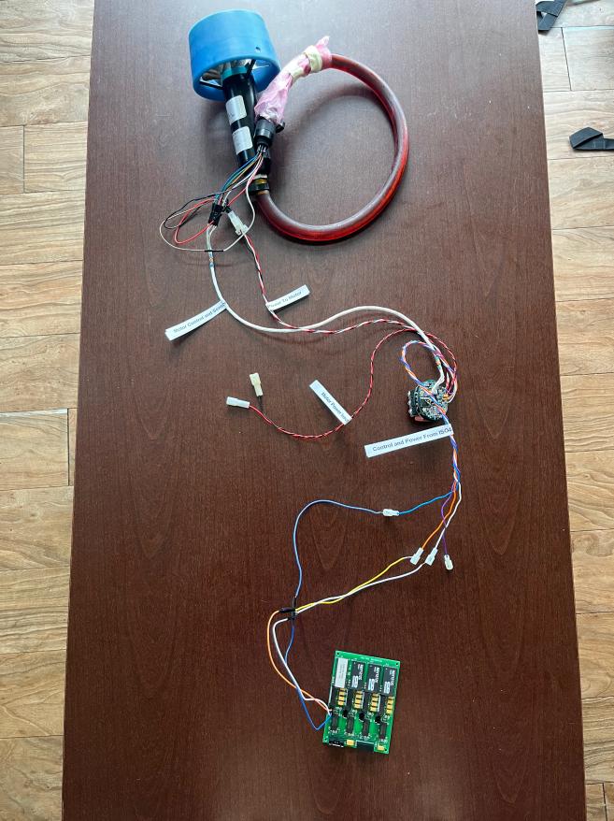
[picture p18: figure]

Figure 21. The wiring for the power subsystem is connected to the subsea thruster. (team-fig)

The electrical subsystem was not physically integrated into the model, despite having a space set aside in the CAD, because an atmospheric pressure vessel, or “bottle,” needs to be designed to properly hold the electronics. This is a matter for future teams.

Testing/Verifying/Validating/Experimental Plan

The three areas the team looked into for testing, verifying, and validating were the 6 degrees of freedom of the ROV, the overall strength of the ROV, and the power of the thrusters.

Testing the number of degrees of freedom the ROV has was performed in Desmos by determining the net force and torque vectors given different power and direction inputs to the four thrusters. An Excel spreadsheet was also utilized to calculate the resultant force and torque vectors given thruster positions and output forces. Figure F.1. shows the Excel spreadsheet and the resultant forces and torques when all four thrusters are pointing forward and outputting 1 lbf of thrust.

To test the strength of the build, the team simulated different forces in Solidworks. Because the CAD model had every fastener and bolt modeled, the simulations had to use a simplified model because there wasn’t enough memory in the computer to simulate the stresses in every bolt. Figure 22 below shows the stress-strain curve of 5052 aluminum. The elastic region of 5052 aluminum ends at roughly 175 MPa, meaning the stresses in the CAD model must be below 175 MPa so the frame returns to its original shape.

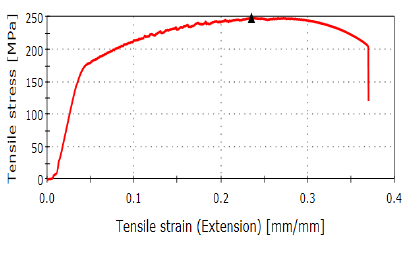
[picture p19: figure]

Figure 22. Stress/strain curve for 5052 Aluminum

Figure 23 shows the heat map for a 50-pound force acting on the thruster clamp acting downward with the thruster arm horizontal. The ROV will rarely experience a 50-pound force in the perpendicular direction to the thruster arm. The only time this could happen is if the ROV impacts an external object. As can be seen by the legend bar on the right, the maximum stress experienced by the frame is 151 MPa, well below the 175 MPa limit. If the ROV impacts something that causes a greater than 50-pound force onto the thruster arm, the point of failure is the bolts connecting the thruster arm to the rotary actuators. These bolts would shear, preventing lasting damages from affecting the expensive thrusters or rotary actuators. If this were to occur, the thruster would be shut down and the ROV would return to the surface for repairs.

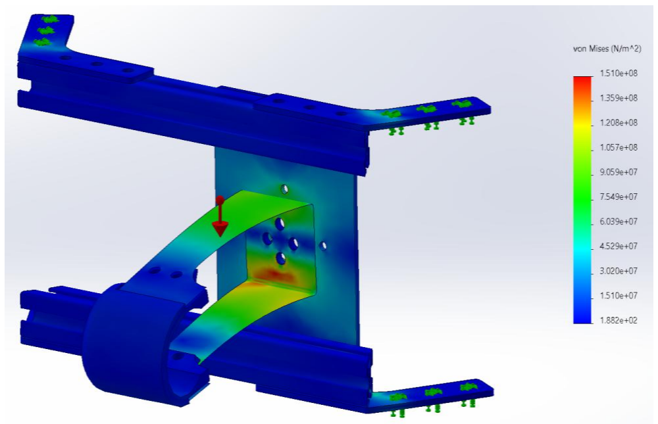
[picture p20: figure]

Figure 23. Stress heat map for a 50-pound force acting on the thruster clamp acting downward with the thruster arm horizontal (team-fig)

Figure 24 shows the stress heat map for a 90-pound force acting on the thruster clamp acting downward with the thruster arm vertical. As can be seen from the heat map legend on the right, the highest stresses experienced by the ROV frame are in the 150 MPa range, which is less than the critical 175 MPa stress value. The thruster arm would experience this force when the thrusters are in reverse. The maximum force the thrusters can output in reverse is 8 pounds, meaning the frame and thruster arms are easily able to withstand that force.

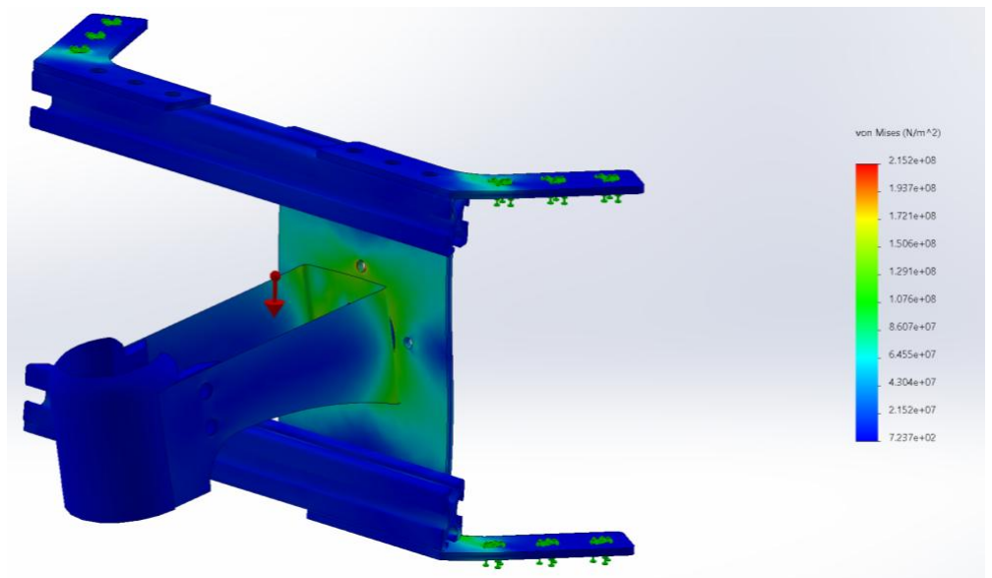
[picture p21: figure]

Figure 24. Stress heat map for a 90-pound force acting on the thruster clamp acting downward with the thruster arm vertical (team-fig)

Lastly, the team tested the thrusters to ensure their functionality. The thrusters required 300 VDc at 1.5 Amps each to operate at full capacity, however, the highest power output the team could find on campus was the Zach Common Labs power wall which could output 120 VDc at 5 Amps. Tecandyne assured the team that powering the thrusters at 120 Vdc for a short period would not significantly damage them. The team attempted to test the thrusters at the power wall, however, as this was the first time the team used the power wall, a supervisor needed to be present. The supervisor who would’ve helped the team was not around during the testing time, so the team was unable to test the thrusters. This unfortunately leaves the testing of the thrusters to the following team.

Safety/Hazard Assessment and Evaluation

Ensuring the safety of the subsea ROV and its operators was a primary concern throughout the design, construction, and testing phases. One of the earliest discussions centered around safety during the construction stage, particularly during material cutting and shaping. These tasks posed the highest risk of physical injury and were therefore conducted exclusively in the FEDC workshop under the supervision of trained personnel.

Operational hazards associated with the ROV primarily relate to its electrical systems and propulsion mechanisms. The ROV is equipped with high-powered thrusters capable of generating significant force to maintain consistent underwater movement. However, this force can present injury risks if proper precautions are not taken. Additionally, the electrical components of the ROV must be thoroughly insulated to prevent exposure to water and mitigate the risk of electric shock during wiring or testing operations. Ensuring secure, waterproof connections and eliminating loose wiring are critical steps in reducing the potential for electrical hazards from the tether or onboard systems.

From a mechanical safety standpoint, it is imperative to maintain a clear area around the thrusters at all times. Foreign objects caught in the propulsion system can cause damage to both the thrusters and surrounding equipment, or lead to breakage due to the high rotational force of the blades.

To address these concerns, comprehensive risk mitigation strategies must be implemented throughout the lifecycle of the ROV. During construction, this includes careful attention to electrical safety, such as ensuring intact insulation, proper grounding of conductive components, use of personal protective equipment, and adherence to established safety protocols. During testing, regular inspections for signs of wear, damaged insulation, or loose wiring are essential. Maintenance procedures should be followed rigorously, and all ROV handling should occur in dry, controlled environments. In addition, operators should undergo thorough safety training.

To minimize risks associated with the thrusters, it is essential to keep them free from obstruction. If an object becomes lodged in a thruster, power to the system must be cut immediately. The obstruction should be removed carefully using non-conductive tools, such as a plastic or rubber-handled screwdriver, to ensure the safety of the individual performing the task.

Through consistent application of these precautions and practices, the safety of both the ROV and its operators can be significantly enhanced during all phases of its operation.

Reliability Assessment

With a multitude of interfacing components and moving parts being used in a harsh environment such as the deep ocean, reliability is an important design consideration to implement into the engineering process. A common set of factors that tradeoffs regarding ROVs in the industry are the number of parts, number of repairs, time working, and time being repaired. ROVs are only useful when they are engaged in working tasks, which leaves repair periods, surfacing, and submerging as non-profitable time. This means designing the ROV in a way that is conscious of the time (and profit) that is lost due to the ROV surfacing, being maintained, and submerging again.

One potential design concern with this next-generation ROV (Remotely Operated Vehicle) is the outward protrusion of its thrusters. While this configuration may provide improved maneuverability and thrust efficiency, it also introduces a significant operational risk, especially in complex underwater environments. In scenarios such as offshore oilfield operations, ROVs are often required to navigate in close proximity to pipelines, the seabed, coral reefs, or other submerged structures. During these missions, the ROV may need to descend to the ocean floor to perform maintenance, inspections, or repairs on pipelines and related infrastructure.

In such settings, the exposed position of the thrusters could make them vulnerable to accidental contact with underwater obstacles. Collisions could occur either during descent, repositioning, or while operating in tight spaces. This contact could damage the thruster components—such as the propeller blades or motor housings—or, worse, lead to debris becoming lodged within the thruster mechanisms. Over time, repeated or unnoticed impacts could degrade performance or cause complete thruster failure.

Should one or more thrusters become inoperable, the ROV’s ability to maneuver effectively would be compromised. In severe cases, the unit might become immobilized or irretrievably stuck in difficult terrain, posing a serious risk to mission success and asset recovery. As such, careful consideration of thruster placement, the addition of protective shielding, or implementing smart collision-avoidance systems may be necessary to mitigate these risks and ensure operational reliability in complex underwater environments.

Societal Factors and Impact

The subsea ROV brings several significant impacts, both positive and negative. ROVs are primarily used to conduct inspection and maintenance on offshore oil and natural gas rigs, as the depths are too extreme to be traversed by piloted watercraft. The oil and gas industry is critical to everyday life, with fossil fuels being the source of power for most everything used and interacted with daily. The ability to increase the efficiency that work is done on these rigs to ensure that procurement of our most important resources is not inhibited allows for more security in the things that all people interact with to be working more efficiently in every way. Being able to use the ROV’s improved dexterity and visibility to pick up on issues with drill equipment will have a positive effect on the safety of the operators on the rigs, if faults are able to be detected earlier and more easily and frequently, allowing them to be corrected before a major failure causes a disaster that puts operator lives at risk as well as major environmental damage in prevention. The world of marine research may be able to benefit from an ROV that can reach more difficult environments to provide us with greater knowledge of the oceans that surround us.

The ability to move, observe, and perform tasks underwater much like a human diver presents a major advantage: it can potentially replace the need for divers in many operations. While divers are not currently employed to work on offshore equipment at extreme depths, the ocean is an inherently dangerous environment. ROVs are a way to eliminate the risks associated with sending people underwater with oxygen tanks, such as decompression sickness, equipment failure, or other life-threatening hazards. The next-gen ROV will be able to function much more parallel to a human diver due to design elements put in place, which could allow for the use of ROVs at shallower depths, keeping more lives out of harm’s way. Additionally, using an ROV could greatly reduce the extensive training, certifications, and preparation normally required for underwater work. This shift could lead to lower operational costs and fewer man-hours spent in hazardous environments.

However, the use of ROVs also carries potential drawbacks. If a malfunction occurs underwater, such as an electrical failure, it could have harmful effects on marine life. An electrical component, if damaged and exposed to the surrounding water could injure, disorient, or even kill nearby wildlife, particularly species that are highly sensitive to electric fields. Beyond environmental impacts, there are also social and economic considerations. As ROVs take over tasks traditionally performed by divers, professional divers may face reduced job opportunities, leading to economic displacement in industries that have long relied on human expertise underwater.

Future Work

This project is a multi-year endeavor, so future work is already laid out. The main components have had design input by the end of the 2024-2025 year. The future groups will be refining designs for the camera system, manipulator, chassis, and propulsion system to come together functionally with an optimized skillset. The main tasks that will follow this year are systems engineering and systems and component integration. The meat of the electronics is still to be designed, with providing power to the components on the ROV itself. Creating a tether system that works well and doesn’t interfere with the design requirements is also a need, as well as determining the system for tracking buoyancy and stability automatically, and relaying info through the tether to the operator via the cameras and other sensors. The thrusters must be paired to work together, as well as the manipulator must be programmed to function to industry expectations. Much more is to be done to see this ROV project through. Making the many parts of the ROV work together will pose quite a challenge to the coming groups, but with the resources available at Texas A&M it should have an impressive outcome.

Table 4. Future work areas that will be covered in coming years

System or Sub-System | Area of Work | Need | Comment
Directional Control | Control Systems | Will need to create a system that connects the operator to the rotary actuators and thrusters. | Critical to the design requirements of the capabilities of the human-like next-gen ROV.
Manipulator Control | Control Systems | Will need to design the placement of the manipulator on the ROV chassis and its electronics. | Necessary for expected ROV industry functions.
Camera Control | Control Systems | Will need to progress on the mounting, circuit, and system design of the 360-degree visibility characteristic of the ROV. | Also critical to the design requirements of the next-gen ROV.
Connecting Components & Systems | Systems/Component Integration | Items such as interfacing the cameras with the VR headset, working each thruster together, the tether to the operator and ROV, the manipulator to the ROV, etc. | Most likely be a large chunk of the phase it is part of.
Testing Connections | Systems/Component Integration | Testing the tether functionality and ability | Important to determine failure points

| | to allow mobility and not restrict. Testing thruster/rotary actuators under stressful inputs. Testing manipulator/ROV connection under stressful inputs. | throughout the ROV.
Thruster Operation | Operational Testing | Test the operation of the thrusters at various voltages. | The thrusters are 18 years old and need to be tested to ensure their functionality.
Camera Operation | Operational Testing | The camera and operator viewing must be tested to ensure the 360-degree field of view. | Data transfer between the ROV and the operator must be accurate, reliable, and fast.
Control Functions | Operational Testing | The controls of the ROV must be tested to ensure the ROV meets the customer's requirements. | Real testing of complete subsystems begins.
In-water Testing | Performance Testing | ROV must be put through the paces to be proven as an underwater craft capable of completing tasks in harsh environments. | This is the final stage of the project. Will be the culmination of all aspects.

Team and Project Organization, Planning, and Execution

The team adopted several different strategies to organize, plan, and execute our project. Flexible but defined roles were implemented in team management and organization, as well as in the design process. Task organization used both a WBS and a Gantt chart, as well as dividing up the tasks based on the design roles. Communication consisted of standard messaging applications such as SMS text, and email for quick and informal information. Email was also used to communicate with vendors, sponsors, and other parties providing information, with team members CC’d consistently to ensure all were provided key information as the semester progressed. Microsoft Teams as well as Google applications were utilized to store files and provide new information to all team members.

Team roles were defined as the following set. David Scott was the primary team lead on the organizational side, primarily concerned with communication with sponsors and parts ordering as well as scheduling. On the design side, he helped with the manufacturing, though this came second to duties as team lead. Marcus Navas was the CAE lead organizationally and in charge of the CAD design; two tasks which overlap considerably. Most of the CAD images present in this document are from him. Heath Garett was in charge of financial documentation and planning organizationally and his design focus was the frame. Bobby Clukey was the minute/note taker for meetings, did much of the assembly, and helped with the CAD design, as well as the propulsion subsystem. The first set of duties was more prominent at the beginning of the semester, and the second set towards the end. Finally, Eric Bauman was in charge of the electrical systems design-wise, and did additional administrative tasks organizationally. These tasks were often scheduling and inquiries related to the electrical systems. Although these were the main areas of focus for each team member, the exact roles blended throughout the capstone to allow team members to learn multiple different aspects of the ROV.

The team used both a WBS and a Gantt chart to create an outline of tasks for the two-semester process. These documents are presented here:

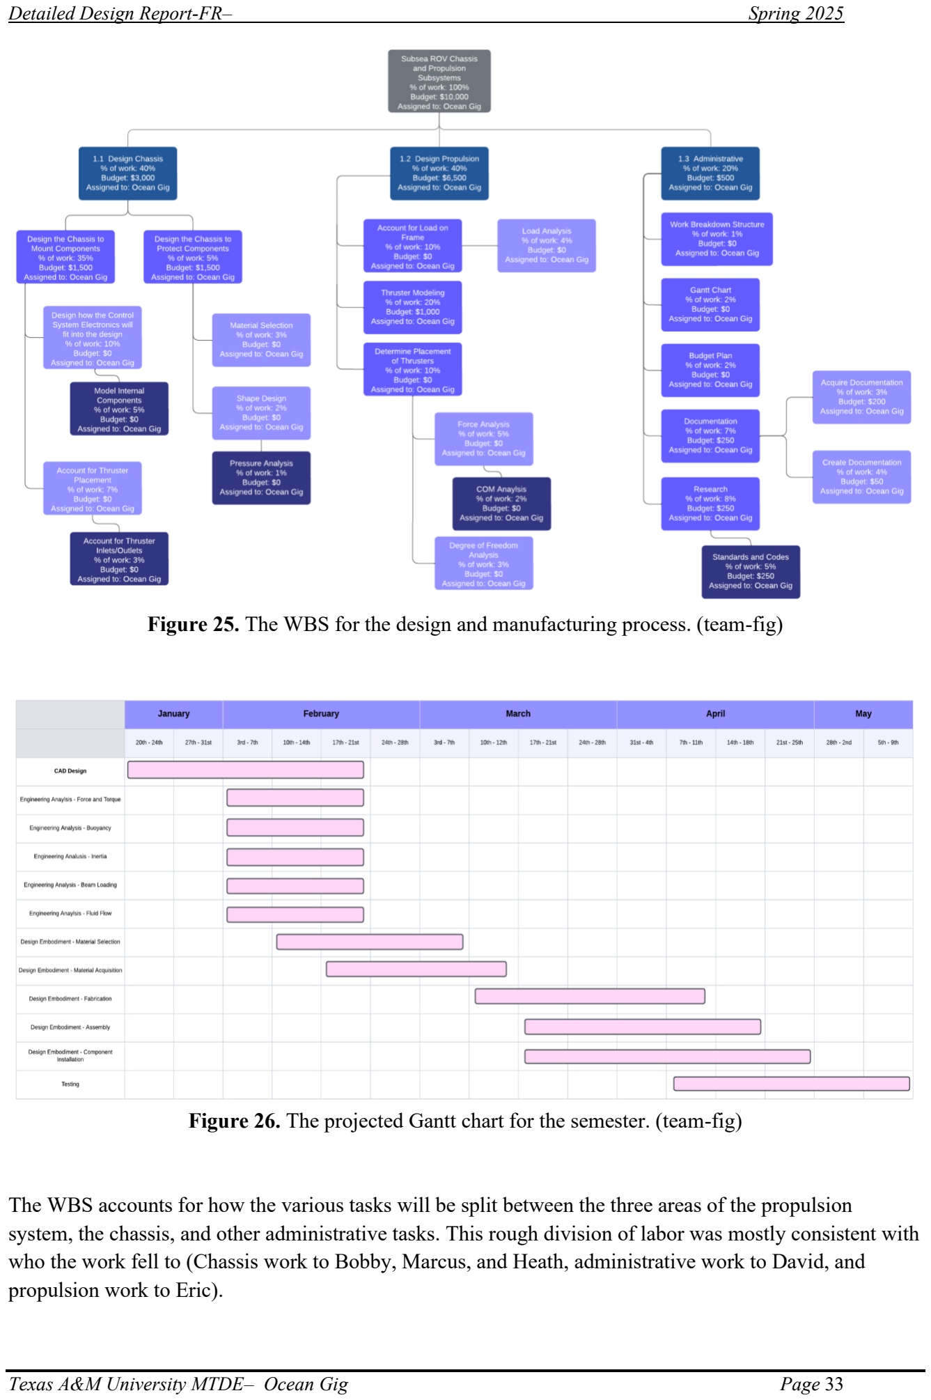
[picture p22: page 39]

Figure 25. The WBS for the design and manufacturing process. (team-fig)

Figure 26. The projected Gantt chart for the semester. (team-fig)

The WBS accounts for how the various tasks will be split between the three areas of the propulsion system, the chassis, and other administrative tasks. This rough division of labor was mostly consistent with who the work fell to (Chassis work to Bobby, Marcus, and Heath, administrative work to David, and propulsion work to Eric).

The Gantt chart shows the projected tasks to be done in the semester in a slightly different format, with time to complete and ordering accounted for. The term “projected” is used because the actual execution of these tasks often fell at different times than the ones presented on the chart, especially towards the end of the semester. The actual dates for some of these tasks are shown here:

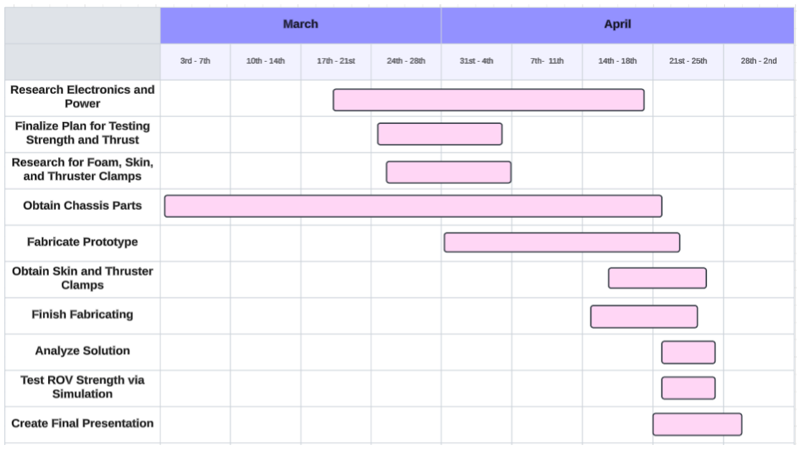
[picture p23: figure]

Figure 27. The actual completion times for tasks are between March and April. (team-fig)

As is visible in this chart, the procurement of the parts to assemble the chassis took much longer than expected, nearly a month and a half. This caused delays in several other areas of the project, most notably assembly. While the Gantt chart from the beginning of the semester was a good starting point, it did not account for unknown potential delays beyond what it had accounted for, requiring flexibility to complete what we completed on time. This delay in the procurement of parts caused the fabrication and testing of the ROV to be significantly constrained in time.

Most work meetings were conducted during studio time, including sponsor meetings, organized by David, with Bobby as a note-taker. When not in those meetings, organization and communication were accomplished over email, through text, or use of the messaging platform Discord.

Summary

When divers operate underwater, they encounter numerous hazards inherent to the environment. To reduce these risks, underwater remotely operated vehicles (ROVs) have been developed to minimize the need for direct human involvement in dangerous conditions. However, current ROVs lack the ability to move and perceive their surroundings with the same flexibility and precision as a human diver. The objective of this project was to develop an ROV capable of replicating diver-like movement and performing tasks typically executed by divers. The specific focus for this team was the design and construction of the chassis and propulsion systems.

At the start of the semester, preliminary progress had been made in computer-aided design (CAD), and many analytical aspects of the project had been outlined. However, all work up to that point remained theoretical, with no physical components assembled. The only available hardware consisted of thrusters that had been generously donated, as well as the electronics to power these thrusters.

This report presents the analytical diagrams and charts used to identify critical needs, functions, and design solutions that contributed to the development of the final product. It also includes financial documentation to confirm the project remained within budget, along with a detailed overview of the ROV’s construction process.

The completed project resulted in a fully built ROV chassis with thrusters capable of providing six degrees of freedom. This configuration enables the ROV to maneuver through water in a manner that closely simulates the movements of a human diver. With this completed model, the team was able to test the 6-degrees of freedom of the ROV, the strength of the ROV, and attempted to test the force output of the thrusters given different power inputs.

To achieve a functional prototype, the next team in the capstone will perform control analysis using the thrusters and rotary actuators and the final team will perform system integration to ensure the visual, chassis, propulsion, and manipulator subsystems all work together. The team was unable to test the thrusters because of complications with the supervisor, meaning the controls team will need to perform the tests on the thrusters.

Special recognition is extended to Professor William Ledbetter and Mr. Don Wells for their generous support throughout the project, and to Dr. Andrew Conkey and Professor Oscar Lopez for their assistance throughout the capstone project. Appreciation is also given to members of Oceaneering International, Inc. for their valuable insights and willingness to share their expertise in subsea ROV technology.

Appendix

A. List of Abbreviations and Terminology

CNC: Computer Numerical Control

DOF: Degrees Of Freedom

FAD: Function analysis diagram

Full Depth Rated: Rated to withstand the pressures at the bottom of the Marianas Trench, the deepest part of the ocean.

Propwash: The effect that thrusters have on the fluids passing through them. This effect makes the fluids rotate in a spiral pattern after passing through the propeller.

ROV: Remotely Operated Vehicle

SWOT: Strengths, Weaknesses, Opportunities, and Threats

Tether (Umbilical): The wired connection between the ROV and the pilot on the surface which powers the ROV and controls the thruster directions and powers.

WBS: Work Breakdown Structure

B. References
[1] Oceaneering International, 2024, “Analyzing the Ocean Gig Prototype Design in Relation to Current Industry Standards.”
[2] International Marine Contractors Association, 2025, “IMCA International Code of Practice for Offshore Diving,” IMCA.
[3] International Marine Contractors Association, 2023, “Code of Practice for the Safe Use of Electricity under Water,” IMCA.
[4] International Marine Contractors Association, 2021, “Recommended Practice for the Use of High Pressure Jetting Equipment by Divers,” ICMA.
[5] International Marine Contractors Association, 2021, “Remotely Operated Vehicle Intervention during Diving Operations,” IMCA.
[6] International Marine Contractors Association, 2024, “The Safe and Efficient Operation of Remotely Operated Vehicles,” IMCA.
[7] International Marine Contractors Association, 2021, “ROV Mobilisation,” IMCA [Online]. Available: https://www.imca-int.com/resources/technical-library/document/04883c5f-c55b-ee11-8dee-6045bdd0ef45/

[8] American Society for Testing and Materials, 2025, “Design and Operation of Subsea Production Systems,” ASTM.
[9] American Society for Testing and Materials, 2025, “Remotely Operated Tools and Interfaces on Subsea Production Systems,” ASTM.
[10] American Society for Testing and Materials, 2025, “Recommended Practice for Subsea Structures and Manifolds,” ASTM.
[11] American Society for Testing and Materials, 2025, “Recommended Practice for Analysis, Design, Installation, and Testing of Safety Systems for Subsea Applications,” ASTM.
C. Order of Magnitude and Detailed Calculations

Figure C.1. Calculations of Archimedes’ Principle in SolidWorks. (team-fig)

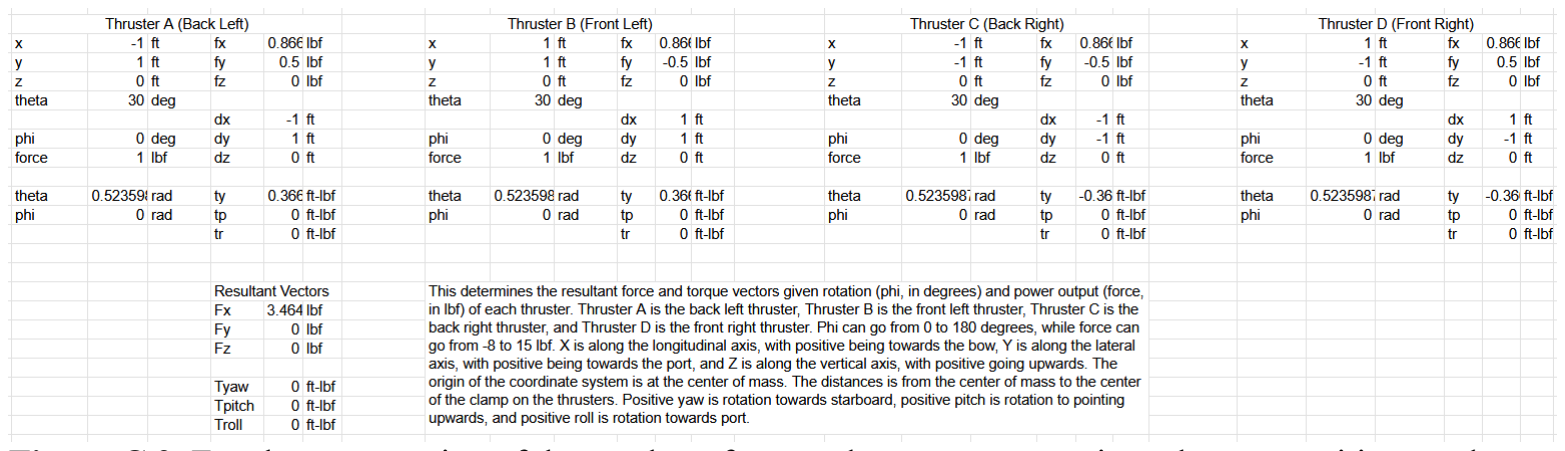
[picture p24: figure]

Figure C.2. Excel representation of the resultant force and torque vectors given thruster positions and output forces. This instance shows the resultant forces and torques when all four thrusters are pointing forward and outputting 1 lbf of thrust. Enlarged image shown in Figure F.1. (team-fig)

E. Detailed working drawings/models/assembly

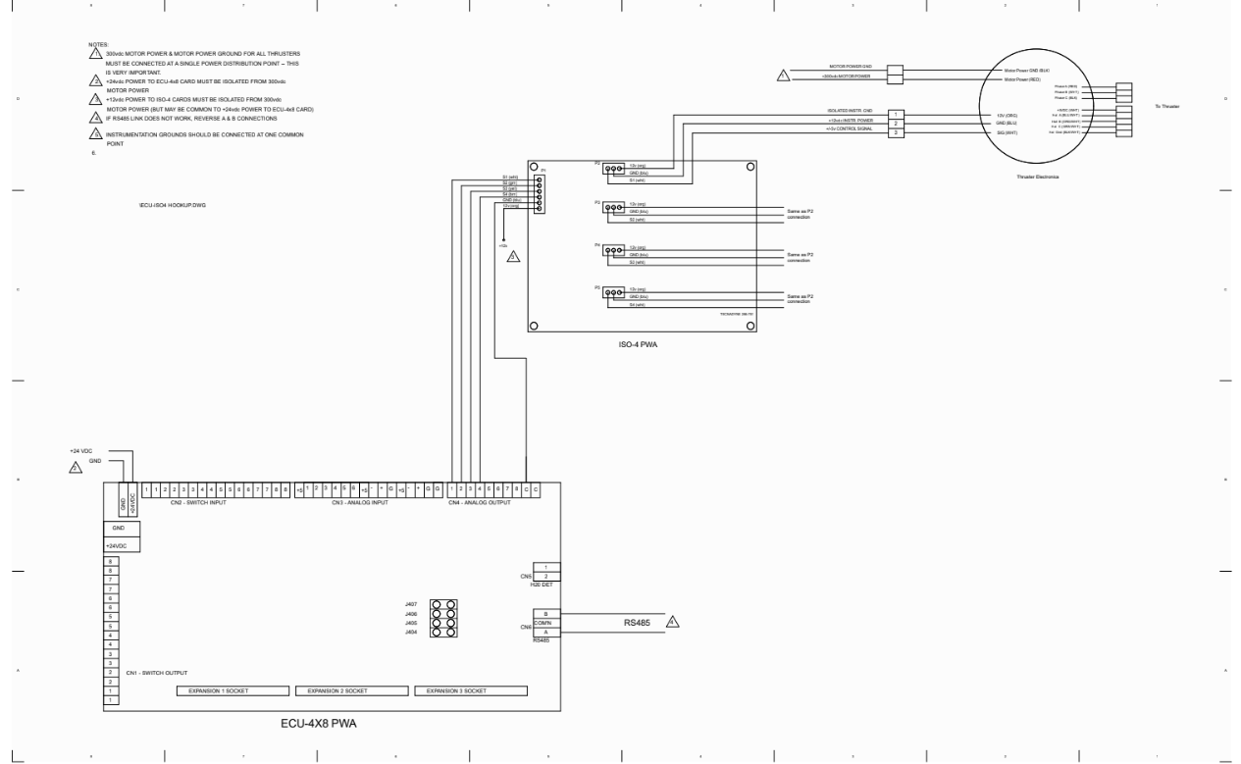
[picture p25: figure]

Figure E.1. Enlarged model of the wiring diagram for the thruster power and control system

F. Testing/Validating/Verification/Experimentation

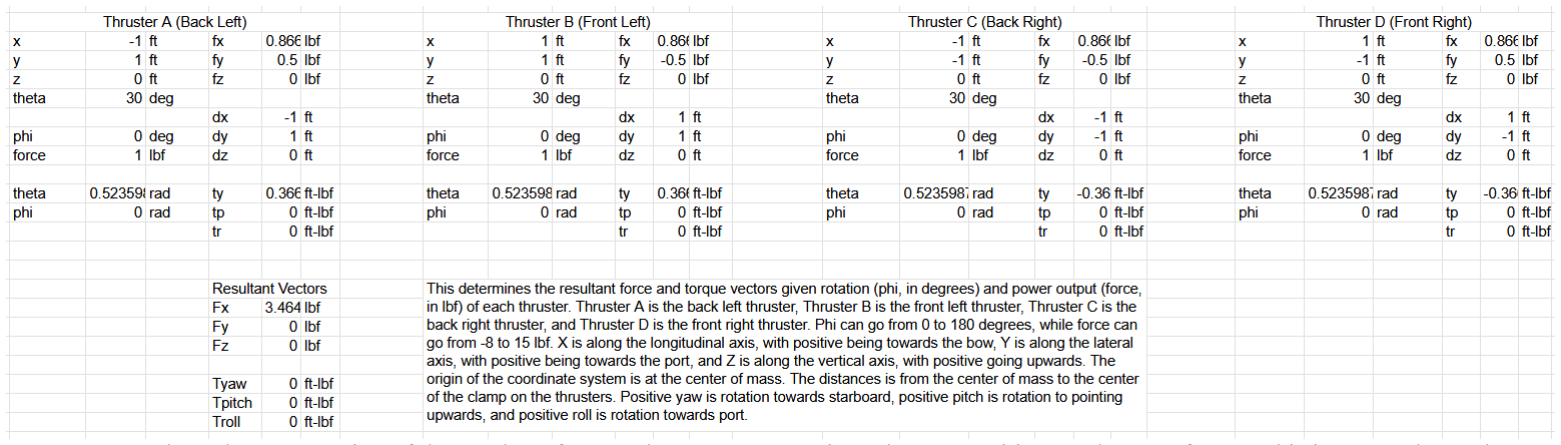
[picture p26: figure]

Figure F.1. Enlarged representation of the resultant force and torque vectors given thruster positions and output forces. This instance shows the resultant forces and torques when all four thrusters are pointing forward and outputting 1 lbf of thrust. (team-fig)

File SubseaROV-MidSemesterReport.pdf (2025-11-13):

## Embodiment Design Report Subsea ROV

## Prepared For Mr. William Ledbetter Mr. Don Wells


## Presented to Instructors: Dr. Andrew Conkey Oscar Lopez, MSCE, P.E., Professor of Practice Sponsor: Mr. William Ledbetter Mr. Don Wells

## Prepared by: Ocean Gig Eric Bauman Bobby Clukey Heath Garrett Marcus Navas David Scott

## Texas A&M University Department of Multidisciplinary Engineering

## ITDE 401 Interdisciplinary Design FALL 2024 – Sections 900/M02

## November 22, 2024

Texas A&M University-MTDE – Ocean Gig | 2

### Executive Summary

Summarize the project for the semester within two pages (ideally, one page). This includes the design steps taken to reach your final point in the project. Essentially, you need to address:
- What was the need
- What are the top-level functions and specifications
- What was finally opted for
- Future goal of team regarding the project
- Note of thanks to the sponsors

Whenever divers work underwater, they put themselves at risk of injury and death. Because of this, divers are only able to safely work at about 100 meters, and most deepsea infrastructure is much deeper than that. There is a need to replace these divers to take them out of the risky scenarios while maintaining the capabilities of a human diver. The current models of subsea ROVs are big, expensive, and unmaneuverable. To make an ROV similar to that of a human diver, it must be smaller, able to fit in the same size holes and areas that a diver can, and be able to swim like a diver could underwater.

A special thanks goes to Mr. William Ledbetter and Mr. Don Wells for their generous support in helping the team with their work in working on the project. Thanks also must be given to the members of Oceaneering International, Inc. for their willingness to talk with the team about subsea ROVs and their experiences in the industry.

Texas A&M University-MTDE – Ocean Gig | 3

## Embodiment Design Report

### Table of Contents

Executive Summary | 1
List of Figures and Tables | 3
Glossary | 4
-Introduction | 1
-Need Statement and Analysis | 2
-Quality Functional Diagram (QFD) | 3
-Background and Design Research | 6
-Function Structure | 8
-Design Specifications Table | 9
-Overall Expected System Description | 12
-Concept Generation and Analysis: | 14
Design Embodiment | 17
-System Description | 17
-Human Factor Engineering | 17
-Engineering Analysis | 17
-Failure Mode and Effect Analysis | 18
-Cost Estimation | 18
-Work Breakdown Structure Semester II | 19
Summary | 23
A. List of Abbreviations | 24
B. References | 24
C. Order of Magnitude and Detailed Calculations/Analysis | 24
D. Concepts Entertained | 25
E. Down Select | 25
F. Detailed working drawings/models/assembly | 25
G: Cost Estimation Details | 25

{ The intent of this report is for the design team to present the application of the top down design methodology to this course to their specific project.
All sections need to have an introductory paragraph the maps out what that section covers. Note content in this report is parallel to has been asked for through the term. However, teams are encouraged to reevaluate what was put into that report before blindly copying and pasting into this report.
NOTE: Remove the bold text in the {} from your submitted report}


Texas A&M University-MTDE – Ocean Gig | 4

### List of Figures and Tables

The list is to be broken up into two sections. One for figures and one for tables. Can use the “auto” generate feature in Word (can be tricky to use). Be sure that figure no. and page no. match.

Figure 1. Chassis subsystem House of Quality


Texas A&M University-MTDE – Ocean Gig | 5

Figure 2. Propulsion subsystem House of Quality


Texas A&M University-MTDE – Ocean Gig | 6

Figure 3. Primary Function Structure


Texas A&M University-MTDE – Ocean Gig | 7

Figure 4. The “Death Star” design

Figure 5. The “Box” design


Texas A&M University-MTDE – Ocean Gig | 8

Figure 6. The “Turkey” design

Figure 7. Isometric drawing of The Turkey design. The design will be 24 inches long, 25 inches wide, and 10 inches tall.


Texas A&M University-MTDE – Ocean Gig | 9

Figure 8. The CAD drawing with the Tecnadyne Model 300 thrusters and Tecnadyne Model 20WD rotary actuators labeled.


Texas A&M University-MTDE – Ocean Gig | 10

Figure 9. The Work Breakdown Structure for the project

Texas A&M University-MTDE – Ocean Gig | 11

Figure 10. Gantt Chart for the spring 2025 semester

Table 1. Researched Patents and Trademarks

Patent Document ID | Patent Holder | Publication Date | Patent Name
US 20240101236 A1 | Oceaneering International, Inc. | 2024-03-28 | MODULAR SUBSEA VEHICLE
US 20240383591 A1 | Heliopolis Holdings Limited | 2024-11-21 | UNDERWATER DOCKING STATION
US 20240239457 A1 | Taylor; Shawn Cutri; Alex Nguyen; Khang Yousif; Sarmad | 2024-07-18 | AN UNDERWATER PROBE OR SUBMERSIBLE

Texas A&M University-MTDE – Ocean Gig | 12
| Le; Thanh
US 20240218761 A1 | TLA SUBSEA LTD | 2024-07-04 | APPARATUS, SYSTEM AND METHOD FOR TETHERING A SUBSEA ASSEMBLY

Table 2. Researched Standards, Codes, and Regulations

Code ID | Code Name
IMCA D014 | IMCA international code of practice for offshore diving
IMCA D049 | Code of practice for the use of high pressure jetting equipment by divers
IMCA D045/R015 | Code of practice for the safe use of electricity under water
IMCA R004 | The safe and efficient operation of remotely operated vehicles
IMCA D054/R020 | Remotely operated vehicle intervention during diving operations
IMCA R009 | ROV mobilisation
API RP 17A | Design and Operation of Subsea Production Systems
API RP 17H | Remotely Operated Tools and Interfaces on Subsea Production Systems
API RP 17P | Recommended Practice for Subsea Structures and Manifolds
API RP 17V | Recommended Practice for Analysis, Design, Installation, and Testing of Safety Systems for Subsea Applications

Texas A&M University-MTDE – Ocean Gig | 13

Table 3. Design Requirements and Specifications
Functi on | Action | Parameter/ Constraints | Analysis Type (Engineering Science) | Comments
1.0 | Develop unique chassis | Reduce size to access tight spots | Structural Analysis, CAD design, fluid dynamics, budgeting | Keep material selection in mind.
1.1 | Accommodate a previously designed visibility system | 360 degree, <100ms latency | Electronics interfacing, energy management, data rate, processor speed | Focus more on visibility, and its respect to physical systems.
1.2 | Utilize tooling and a manipulator | Receive accessories, operator-friendly interfacing | CAD modeling, material analysis, | Research standardized tools and tasks, and keep mounting consideration in design
1.3 | Utilize materials that provide strength and structure | Maintain positive buoyancy and remain strong at depth | Materials analysis, fabrication, | Should withstand 10,000 ft of depth
2.0 | Equip chassis with efficient propulsion system | Provide 6 degrees of freedom | CAD design, fluid dynamics, Electronics, Energy management | It should be able to move in each direction independently.
2.1 | Integrate 180 degree actuators | Mounted thrusters to rotate 360 degrees | Electronics, control systems, fluid dynamics | Ensure safety mechanisms to protect wiring.
2.2 | Efficiently balance changes in mass | <0.1 second reaction to changes in load between 4 active thrusters | Fluid dynamics, motion control | Incorporate redundancy in case of thruster failure as well
2.3 | Efficiently manage tether | Protect tether; prevent exploration inhibition | Electronics, control systems, fabrication, CAD modeling | Consider improving tether visibility through reflectors or colors.


Texas A&M University-MTDE – Ocean Gig | 14

Table 4. Our Decision Matrix for each design

Table 5. The Risk Priority Number calculations for our Failure Mode and Effect Analysis

Table 6. The cost estimation for the project, including the cost for starting the project over without the items already obtained.

Texas A&M University-MTDE – Ocean Gig | 15

### Glossary

Terms and acronyms that are associated with your project. If it is an engineering measure (specification), provide units.
- Propwash: The effect that thrusters have on the fluids passing through them. This effect makes the fluids rotate in a spiral pattern after passing through the propeller.
- Tether (Umbilical): The wired connection between the ROV and the pilot on the surface which powers the ROV and controls the thruster directions and powers.

Embodiment Design Report – | Fall 2024
Texas A&M University MTDE– Ocean Gig | Page 1

### -Introduction

State the general need for what the inspiration was. Try to present it from the client’s perspective.
Then summarize the design approach used as entailed in this report.

NOTE: Use of qualitative statements, especially in the analysis section, must be kept to a minimum (5 to 10). Overuse of qualitative statements in a section, or sections, will lower the grade in that section by ½ to 1 letter grade for that section

For example, “The heat dissipation was lowered significantly by reducing the ohms of the series pass resistor”. Compare this to “the heat dissipation was reduced from 3.0 Watts to 1.6 Watts by changing the series pass resistor from 0.3 ohms to 0.16 ohms”. The adjective “significantly” just makes the reader ask questions. A mechanical example: “The temperature was lowered a lot by increasing the area of the fins”. This should be written, “The steady state temperature reduced from 153F to 141F when the area of the fins increased from 45 in²

to 63.4 in²
.”

The inspiration for this project was to innovate in the current industry of Subsea ROVs. Our client considers them bulky, unmaneuverable, and somewhat inelegant in their design. They wish to challenge the norms of the industry by creating a rover that is incredibly intuitive to control, and with a wider variety of movement and vision.

The inspiration behind this project is derived from our client’s vision to revolutionize and innovate within the SubSEA ROV industry. Our client perceives current ROVs as bulky, difficult to maneuver, and lacking elegance in their design. Our client seeks to challenge these industry norms by creating a new and unique ROV design.

Their goal is to create a rover that is incredibly intuitive to control, offers a wider range of vision, and has enhanced maneuverability, much like a diver would have. Ultimately, the inspiration for this project was offering alternatives to both divers and ROVs, transforming how industries can choose to operate underwater.

Our client was looking towards diver-like movement, which entails 6 degrees of freedom of movement, meaning the rover can move underwater like a diver. Our client also wishes for our rover to have 360-degree vision, in several axes, for enhanced situational awareness that will lead to more efficient task completion.

### Design Identification and Definition

-Need Statement and Analysis

Now that you have some experience and depth of knowledge of the project and if your team is not comfortable with your original Need Statement, now is the time to make it better. When well written, this is a very good way to let your reader know your thought process. Don’t worry about describing the development of it (i.e. the iterative development of it). Should the team feel that the history is needed, it can be provided in the appendix. Be sure to let the reader know. Simply state what it is, and then analyze it (identify key terms/phrases or performance measures). If your team has multiple elements to examine, present a need statement and analysis for each element. Be sure to clearly identify what the need statement relates to. The need statement should have a one to two sentence lead in, shown as an italicized statement with a follow up statement that leads to the need analysis. The need analysis needs to expand on key words and provide insight to potential means of measuring performance.

Design the chassis and propulsion systems for a subsea ROV, that can be used to replace human divers and fit into tight areas than current models, with consideration of buoyancy, versatile visibility interfacing, and 6 degree of freedom maneuverability.

The subsea ROV project was split up into a 5-year plan. The first year worked on the administrative side of the project figuring out how the ROV should be spaced out throughout the five years and working on the main goal of the project. The second year worked on the vision system, including full 360 degree viewing and a borescope for additional viewpoints. We are in the third year of this project. Our tasks are the chassis system and the propulsion system, which is why the need statement only concerns itself with the chassis and the propulsion subsystems of the ROV.

The ROV will need to have either a positive, neutral, or negative buoyancy, which has been left up to the team to decide during the creation of the chassis and propulsion systems. While the team is not focusing on the vision subsystem of the ROV, the chassis and vision subsystems work together. The chassis must be designed in such a way that it gives the vision system the full 360 degree view that has been worked on. Because the team is working to make the ROV more diver-like, the propulsion system must be able to accommodate for the full 6 degrees of freedom, as human divers are able to move in all translational directions and rotations.

-Quality Functional Diagram (QFD)

Provide an opening paragraph explaining the goal of the QFD (i.e. tie into the Need statement and need analysis and client). Then present the QFD. Should it be too big, break the rooms up and present them individually. This should provide a bridge from the needs to the functions and specifications. Rooms 2, 5, 6, 7 and 8 are probably the most critical rooms to address. Should rooms be limited in information, briefly explain why that might be. The QFD is the go to reference for other areas of this report

The goal of the Quality Function Diagram is to take the clients needs and logically apply them into specific design and engineering requirements for our project. By looking at and comparing the statements, need analysis and functions, the QFD allows us to prioritize subsystems, and address what features correlate with each other, along with comparing it with some features of the competition. Some of the ideas we were looking to address pertain to the ROV’s size, maneuverability, and overall thruster pattern.


Figure 1. Chassis subsystem House of Quality

Figure 2. Propulsion subsystem House of Quality

The QFD starts with room 2, which addresses the needs of the clients. For the chassis, some of the most notable ones are the 360 FOV, and accommodating the thrusters. For propulsion some of the notable factors are having 6 degrees of freedom, and variable thrust. These factors guide the functions that our design should have.

Room 5 addresses the engineering specifications for each subsystem. Some of the notable engineering specifications for the chassis subsystem are depth resistant to 10,000 feet and allow for 360 degree field of view for the vision subsystem. For the propulsion subsystem, some of the notable engineering specifications include being stable in 2+ knots of current and having accurate propulsion for accurate movement.

Room number 6, the large center room, describes the relationship matrix, it describes the relationship between the engineering specifications and the customer requirements. Some of the notable relationships between the customer requirements and the engineering specifications are how the budget has a large relationship with every engineering specification in the propulsion subsystem, because the thrusters and rotary actuators that have been donated or researched are expensive.

Room 7, the block on the bottom, describes the engineering requirements, it utilizes the middle section, and sums and normalizes the relationship matrix in order to determine the percentage importance of various engineering specifications with respect to the importance of the customer requirements. For the chassis subsystem, the most important engineering specifications were being depth resistant to 10,000 feet and maneuverable. For the propulsion subsystem, the most important engineering specifications were accurate vehicle acceleration and reliability.

Room 8, the triangle at the top, shows how each engineering specification correlates to each other. One of the strongest propulsion correlations are controllability and vehicle accelerations, with the chassis correlating tether management and maneuverability, along with depth and water resistance.

-Background and Design Research
Present a summary of research the team conducted to gain a better understanding of the current state of technology on the design challenge. Try to keep to two pages. Potentially, could summarize activity in a table(s) {one table for patent search, one table for general web search, etc}. Including when the research was conducted should map into the design process. That is, early research might be very general whereas later research on analysis is more specific. A more detailed research listing would go into the Appendix B section.

Some of the research the team conducted in order to gain a better understanding of the technology was by looking at the current thrusters we had been provided with by the previous team. We found the specifications and the CAD models that were necessary in order to find the dimensional components to create our design. The team also researched the other electronic components that were obtained by the previous years, such as the Insta360 camera, borescope, and the Meta headset that was used for the VR display, to determine the best methods for mounting the cameras and the borescope onto the ROV for 360 degree field of view.

The team also spoke with Oceaneering International, Inc. to gain a better understanding on the current state of the industry. The talk addressed various issues such as the material selection, maximum payload capacity,, thruster placement specifics, and underwater conditions during subsea work, such as currents and buoyancy. During the presentation, Oceaneering gave insight as to how their current ROVs are able to perform underwater and the process the teams at Oceaneering took to design their ROVs. Oceaneering International gave a better idea on determining what market the team should compete in.

Table 1 and Table 2, below, show the US Patents and US and international Codes, respectively, that the team researched to develop potential designs for the final product. The patent US 20240101236 A1 is for a modular subsea remotely operated vehicle with one section of the ROV that can connect to another section to increase the capabilities of the ROV. The code API RP 17H discusses how connections and interfaces in subsea engineering should be built so ROVs across companies can interface with the valves and connections underwater.

Table 1. Researched Patents and Trademarks

Patent Document ID | Patent Holder | Publication Date | Patent Name
US 20240101236 A1 | Oceaneering International, Inc. | 2024-03-28 | MODULAR SUBSEA VEHICLE
US 20240383591 A1 | Heliopolis Holdings Limited | 2024-11-21 | UNDERWATER DOCKING STATION
US 20240239457 A1 | Taylor; Shawn Cutri; Alex Nguyen; Khang Yousif; Sarmad Le; Thanh | 2024-07-18 | AN UNDERWATER PROBE OR SUBMERSIBLE
US 20240218761 A1 | TLA SUBSEA LTD | 2024-07-04 | APPARATUS, SYSTEM AND METHOD FOR TETHERING A SUBSEA ASSEMBLY

Table 2. Researched Standards, Codes, and Regulations

Code ID | Code Name
IMCA D014 | IMCA international code of practice for offshore diving
IMCA D049 | Code of practice for the use of high pressure jetting equipment by divers
IMCA D045/R015 | Code of practice for the safe use of electricity under water
IMCA R004 | The safe and efficient operation of remotely operated vehicles
IMCA D054/R020 | Remotely operated vehicle intervention during diving operations
IMCA R009 | ROV mobilisation
API RP 17A | Design and Operation of Subsea Production Systems
API RP 17H | Remotely Operated Tools and Interfaces on Subsea Production Systems
API RP 17P | Recommended Practice for Subsea Structures and Manifolds
API RP 17V | Recommended Practice for Analysis, Design, Installation, and Testing of Safety Systems for Subsea Applications

-Function Structure
Provide a brief explanation as to what this section presents. Also provide an explanation as to what FR (function requirement), PR (performance requirement), and CR (constraint requirement) represent. The level of the function structure doesn’t need to go more than three levels (more detailed levels can be presented in appendix if needed) for any top-level function. Your original and more complete function diagram is to be included in the appendix. The primary focus here is to establish what the concepts/alternatives need to do and help define any performance requirements as well as constraints. Note: There are a couple of different ways to present this information. One is a bullet list, or function tree, as shown below. The other is a diagram (as shown in lectures).

Function Tree: (example, can be put into table form or other).
FR 1.0 function description (remember, this must be an action) PR1.0 Associated performance requirement(s)
CR 1.0 Associated constraint requirement(s)

FR 2.0
FR2.1
PR 2.1
CR 2.1

The function structure describes the functions that the design (not the design team) must accomplish to meet the need. It guides the entire project. The function structure may be presented in organization chart format or outline format as pointed out earlier. The organization chart is usually easier for people to follow, but the challenge is making sure it is readable. Organization chart format is illustrated in the following. The top box contains the need statement with the functions broken down into subsections as shown below. Performance requirements and constraint requirements are identified. More information on these are in the next section. The function tree as shown above, is a little harder to follow sometimes, but is easier to read. The organizational chart, flow diagram, can be broken up into subcomponents and presented if it helps.

Our diagram is primarily split into 2 parts: the chassis and propulsion systems we will be designing for the ROV. The chassis objectives are highlighted by a need to create a shape that allows the vehicle to act as much like a human diver as possible, reflected by top-level criteria of small size and tooling accommodations. The propulsion system is meant to be complimentary to the chassis’ humanlike scale and shape. The operator should be able to manuever the ROV with a mindset similar to that of them being submerged themself. The propulsion system will also be responsible for keeping the ROV stable during tasks, managing changes in mass or environmental factors such as underwater currents.

Figure 3. Primary Function Structure

Design Specifications Table
Provide an introductory paragraph explaining what this section and table represent. This needs to map back to the previous section as well as back to the QFD.
Table I, summarizes the design requirements and specifications for this project.
Note:This page is in portrait setting. Explain how the content of the table on the next page was developed. Keep the table on the next page in landscape settings.

Our design specifications table revolves around the two primary functions of the 2024-2025 subsea ROV development phase: chassis and propulsion system development. This table is a representation of the high-level design requirements, and goes into more detail about the lower-level needs that will be met in order to successfully meet the requirements of the need statement. The chassis design will be done with a couple key elements in mind. The functions of current industry-standard light-duty ROVs must be maintained if not improved. This includes structural design that effectively holds necessary components such as electronics and tooling, as well as a manipulator and camera system. A smaller chassis that features the ability to see more in the likes of a human diver allows more information to be collected and difficult spaces to be accessed, keeping divers out of danger and more efficiently completing tasks. The propulsion system is designed to further reflect the ROV’s human-like properties. The mounted thrusters will provide motion in any direction, and the theoretically ability to orient in any way (full inversion may not be realistically necessary).

Note: a “section break” was used to allow the table to appear in landscape mode. Be careful deleting lines.
Table 3. Design Requirements and Specifications
Function | Action | Parameter/ Constraints | Analysis Type (Engineering Science) | Comments
1.0 | Develop unique chassis | Reduce size to access tight spots | Structural Analysis, CAD design, fluid dynamics, budgeting | Keep material selection in mind.
1.1 | Accommodate a previously designed visibility system | 360 degree, <100ms latency | Electronics interfacing, energy management, data rate, processor speed | Focus more on visibility, and its respect to physical systems.
1.2 | Utilize tooling and a manipulator | Receive accessories, operator-friendly interfacing | CAD modeling, material analysis, | Research standardized tools and tasks, and keep mounting consideration in design
1.3 | Utilize materials that provide strength and structure | Maintain positive buoyancy and remain strong at depth | Materials analysis, fabrication, | Should withstand 10,000 ft of depth
2.0 | Equip chassis with efficient propulsion system | Provide 6 degrees of freedom | CAD design, fluid dynamics, Electronics, Energy management | It should be able to move in each direction independently.
2.1 | Integrate 180 degree actuators | Mounted thrusters to rotate 360 degrees | Electronics, control systems, fluid dynamics | Ensure safety mechanisms to protect wiring.
2.2 | Efficiently balance changes in mass | <0.1 second reaction to changes in load between 4 active thrusters | Fluid dynamics, motion control | Incorporate redundancy in case of thruster failure as well
2.3 | Efficiently manage tether | Protect tether; prevent exploration inhibition | Electronics, control systems, fabrication, CAD modeling | Consider improving tether visibility through reflectors or colors.

A brief paragraph or two discussing the main points is appropriate here. The analysis type must be included and need to be meaningful to the parameter. Analysis type should be more than say “heat transfer”. Be more descriptive..i.e. convective heat flow. Or, beam analysis based on deflection. The comments box can provide content such as level of confidence, constraint, or other indicator of level of understanding.

This project utilizes a wide interdisciplinary variety of analysis. Most of these types of analysis will require an accurate CAD model for proper analysis. Fluid dynamics of underwater propulsion systems and Finite Element Analysis will be necessary for optimizing the maneuverabilityof the ROV, along with deflection modeling for the structure and beans within the system. A small amount of analysis, most likely done by hand, is needed to analyze the visibility systems, but will also require an accurate CAD model. Physically budgeting our design is necessary to understand how the chassis and propulsion system will be able to accommodate each other, and be able to undergo scaling as the prototyping and building phases reveal necessary changes. Analyzing these systems through these various lenses, we will have a robust and comprehensive understanding of our design.

-Overall Expected System Description

Provide insight as to what are the key attributes and/or features that the design needs to have. Okay to reference what your client has stated. Identify what are some of the key operational points as well. That is, lay the groundwork for the concept section.

Some of the key attributes for the chassis design are the ability to accommodate the thrusters, the electronic and mechanical components of the ROV, and the vision system. The chassis of the ROV must be able to mitigate the thruster prop wash that comes from thrusters. Propwash is the effect that thrusters have on the fluids passing through them. This effect tends to make the fluids rotate in a helical pattern after passing through the propeller. The helical rotation of the fluids decreases the efficiency of any thrusters that the fluid passes through. Because of this, the chassis must be able to mitigate propwash to keep the thrusters at their optimal efficiencies. The chassis must also be big enough to house the electronic and mechanical components of the ROV while keeping the overall weight of the chassis to a minimum. This means that every part should have a purpose and if the product can be designed with fewer parts while achieving the same outcome, the design with fewer parts should be chosen. One of the main goals of the previous year was to develop a way to have a 360 degree field of view. So while the objective of this team is not concerned with the vision subsystem, being able to incorporate the 360 degree field of view into the final design is an important attribute for the chassis design. Another aspect of the ROV chassis is that the current stage of the ROV design does not require it to be marinized. This step comes in one of the next years of the multi-year design process.

The key attributes for the propulsion system design are from the propulsion subsystem to be economical, have 6 degrees of freedom, and have the ability to resist underwater currents. For the propulsions system to be economical, it must have no unnecessary parts. As stated earlier, every part should have a purpose and the design with fewer parts while having the same outcome should be selected. This will reduce the weight of the ROV and reduce the number of potential failures. Divers underwater are able to swim and rotate in all directions. Meaning if an ROV is to be designed with diver-like capabilities, it must also be able to move and rotate in all directions. Divers are unable to work properly in 2 or more knots of current. For an ROV to be more capable than divers, the ROV must be able to withstand greater currents than divers are able to.

### -Concept Generation and Analysis:

Summarize the process that the team conducted to reach the final concept. This is an abbreviated version of what is in the concept report.

When introducing the problem to the team, the sponsor gave examples of current ROVs, such as the Oceaneering Isurus and Magnum, both of which are cuboid in shape, as well as several abnormally shaped ROVs. The team looked into these abnormally shaped ROVs to determine if there was a possibility of making our ROV unusually shaped.

Our first design, nicknamed The Death Star, shown below in Figure 4, was a spherical ROV with thrusters and cameras surrounding the outer shell to give the full 360 degree field of view and 6 degrees of freedom. While this design had some of the more important customer requirements from the QFD, The Death Star had little room for an arm to interact with things underwater. The design was also significantly heavy for its size as it used six thrusters and therefore was very slow in its movement.

Figure 4. The “Death Star” design

Our second design, The Box, shown below in Figure 5, was similar in shape to the Oceaneering Magnum, but much smaller. This design was able to give us the full 6 degrees of freedom needed, but had some blind spots in the field of view. This design was also not able to fit into the small gaps required of it by the sponsor.


Figure 5. The “Box” design

Our final design, The Turkey, shown below in Figure 6, was shaped like a coffin or turkey. This design gave us 6 degrees of freedom with 4 thrusters, making it much lighter than The Death Star and much smaller than The Box. The design was also able to have 360 degrees of view. The previous team who worked on this project worked on the vision system, and they found that a coffin shaped chassis, similar to our design, gave the best design for 360 degree vision.


Figure 6. The “Turkey” design

With these designs and their capabilities, we created a decision matrix to compare the designs with the customer requirements and engineering specifications. Based on this decision matrix, shown below in Table 4, we chose to move forward with The Turkey design as we found it covered all of the important aspects as required by the customer and most of the functions we specified for the subsea ROV.


Table 4. Our Decision Matrix for each design
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

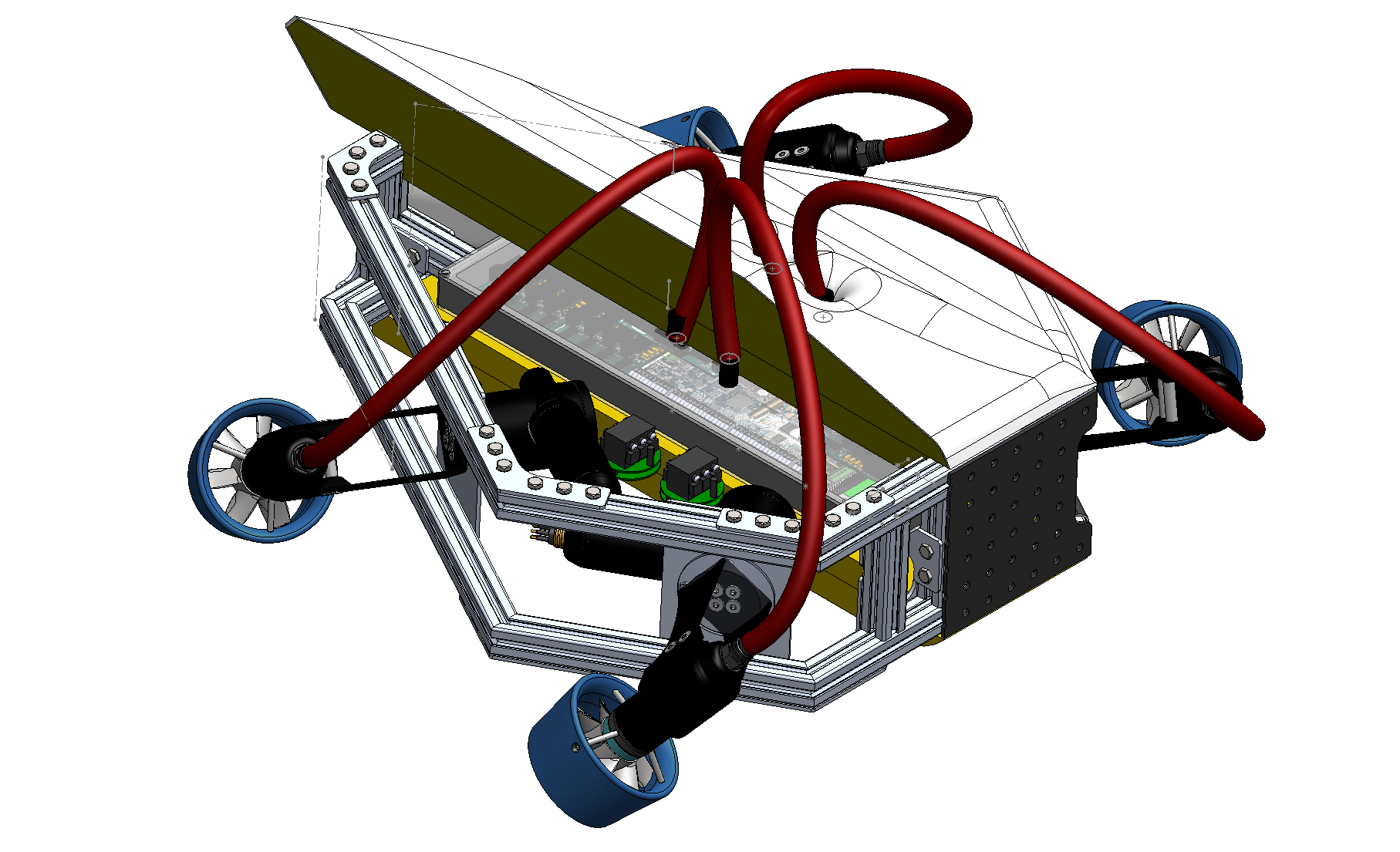
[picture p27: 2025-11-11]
Images-Videos/ROV CAD Cutaway.png

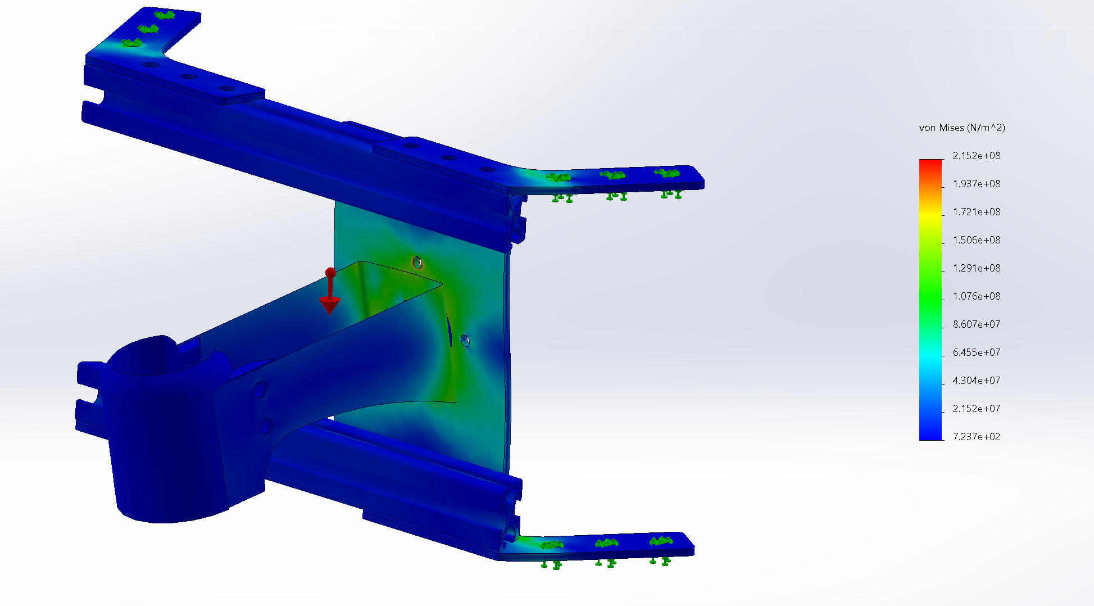
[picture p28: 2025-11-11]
Images-Videos/ROV Force Thrust Simulation.png

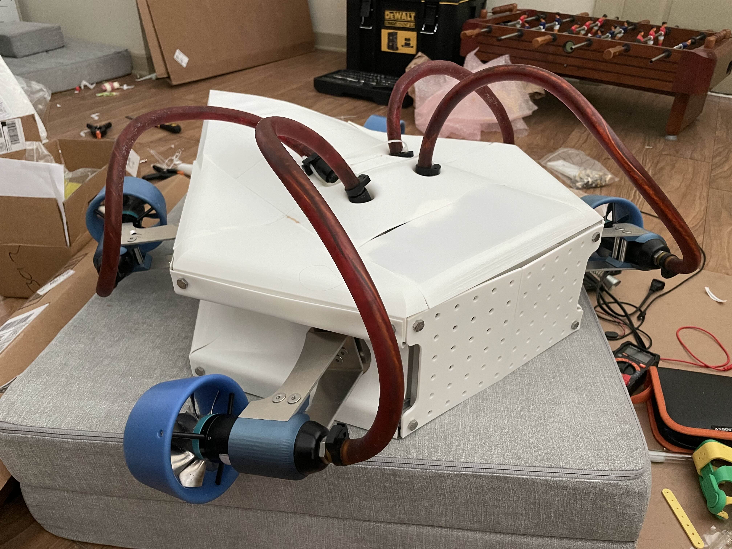
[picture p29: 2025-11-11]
Images-Videos/ROV Model Right.jpg

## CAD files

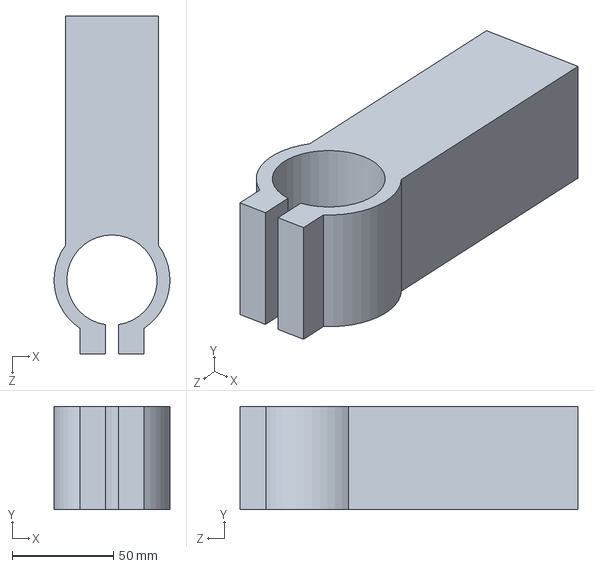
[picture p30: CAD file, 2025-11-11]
CAD Models/ThrusterClampMount.SLDPRT
57.1 x 50.8 x 166.6 mm

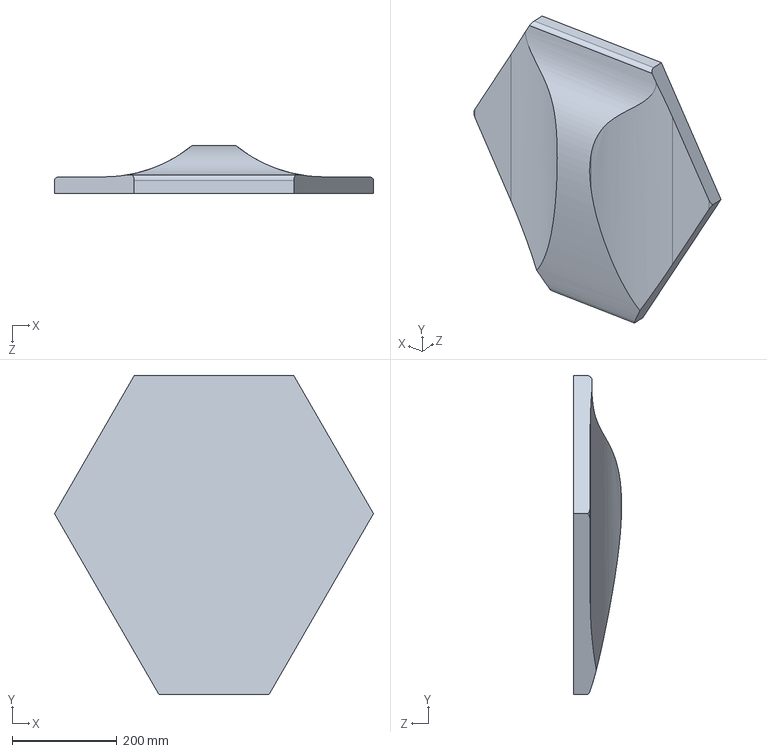
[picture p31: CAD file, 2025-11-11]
CAD Models/TopSkin.SLDPRT
609.6 x 609.6 x 92.4 mm

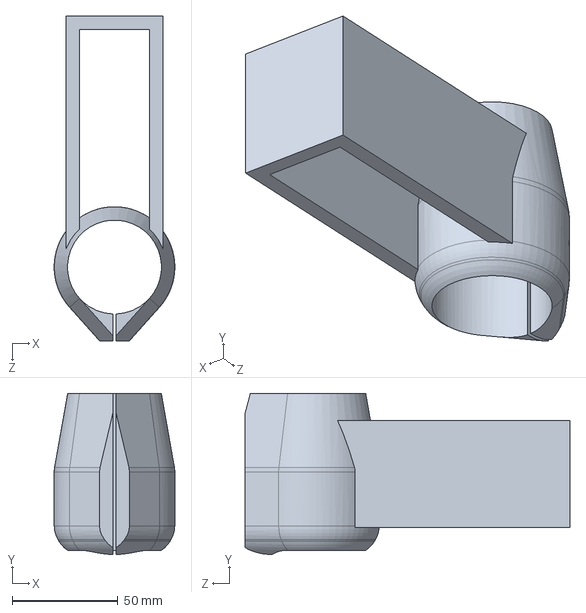
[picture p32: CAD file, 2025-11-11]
CAD Models/ThrusterClamp.SLDPRT
57.1 x 76.2 x 153.7 mm

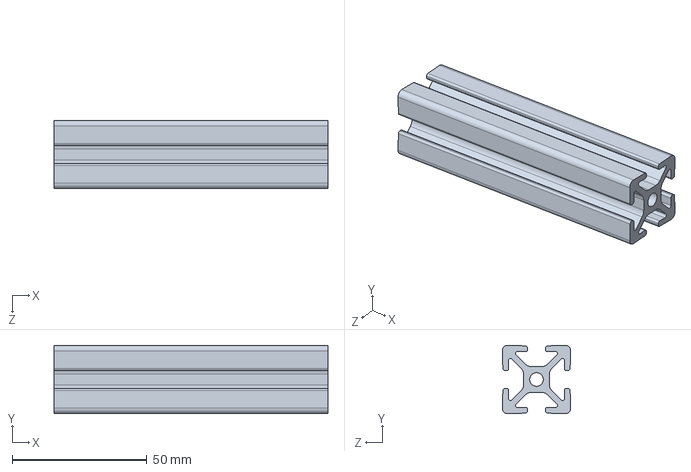
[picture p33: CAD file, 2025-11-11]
CAD Models/RailZ.SLDPRT
101.6 x 25.4 x 25.4 mm

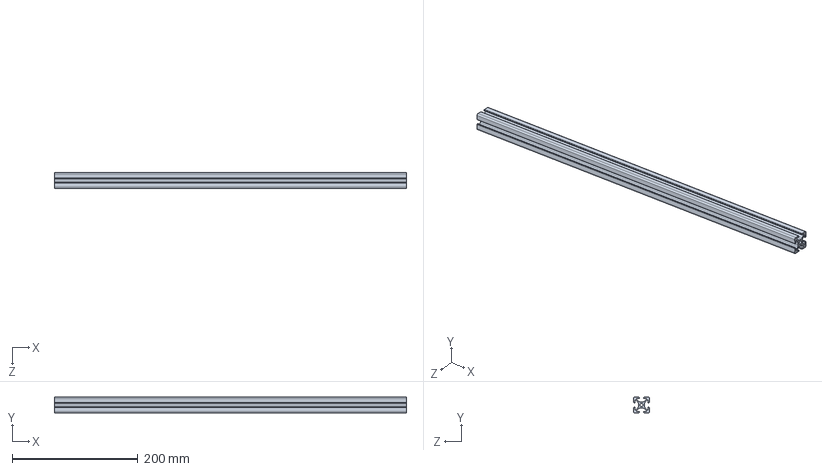
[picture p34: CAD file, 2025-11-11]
CAD Models/RailX.SLDPRT
558.8 x 25.4 x 25.4 mm

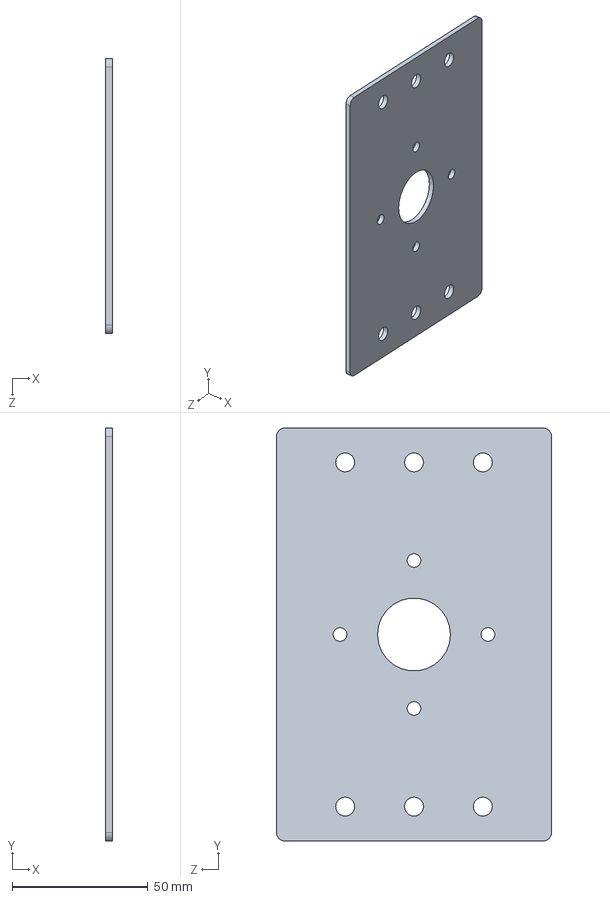
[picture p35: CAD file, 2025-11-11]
CAD Models/RotaryBracket.SLDPRT
2.54 x 152.4 x 101.6 mm

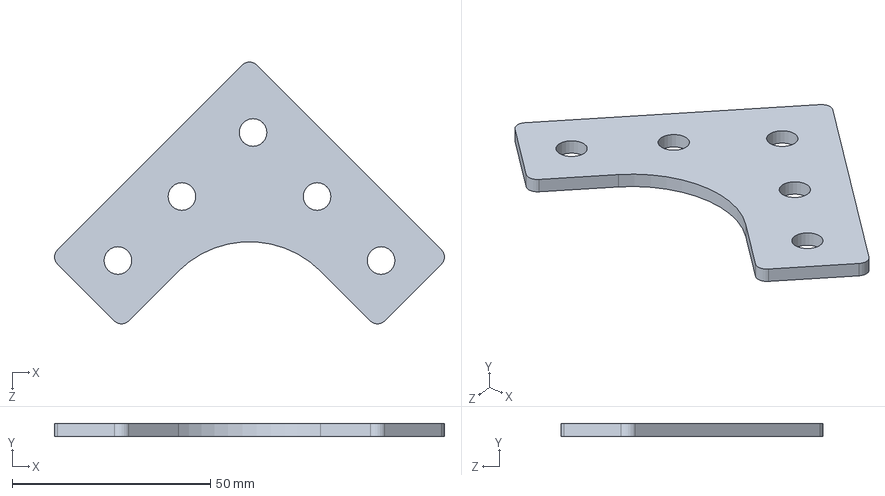
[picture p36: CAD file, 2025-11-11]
CAD Models/Bracket90Short.SLDPRT
98.5 x 3.17 x 66.1 mm

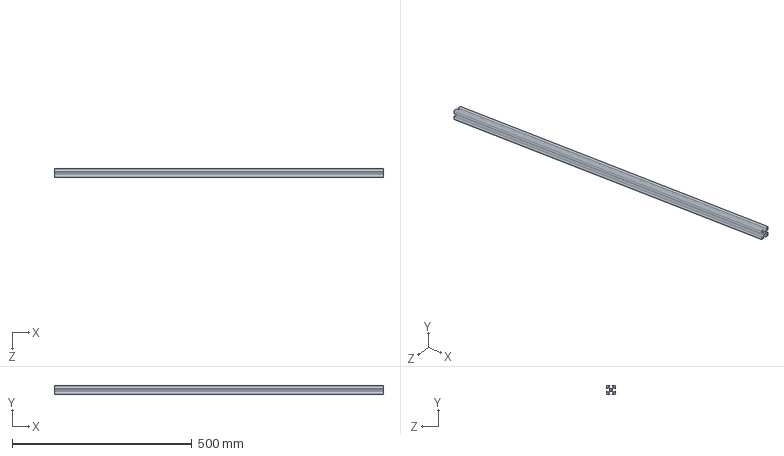
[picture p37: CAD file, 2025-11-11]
CAD Models/RailStock.SLDPRT
914.4 x 25.4 x 25.4 mm

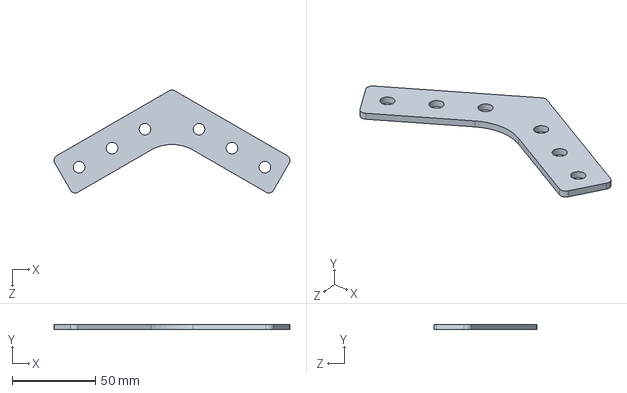
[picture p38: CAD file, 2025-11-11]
CAD Models/BracketAB.SLDPRT
141.9 x 3.17 x 62.0 mm

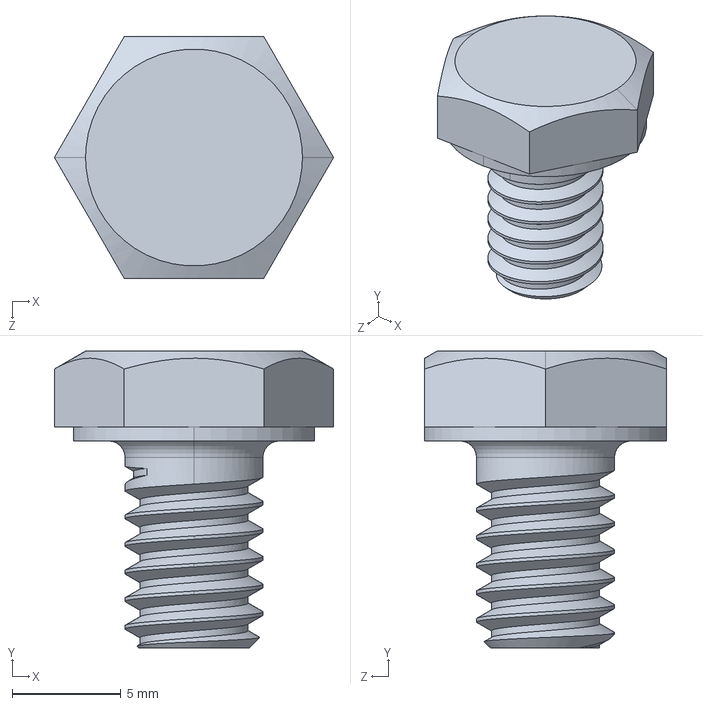
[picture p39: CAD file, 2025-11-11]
CAD Models/fastenal_1170000.sldprt
12.8 x 13.7 x 11.1 mm

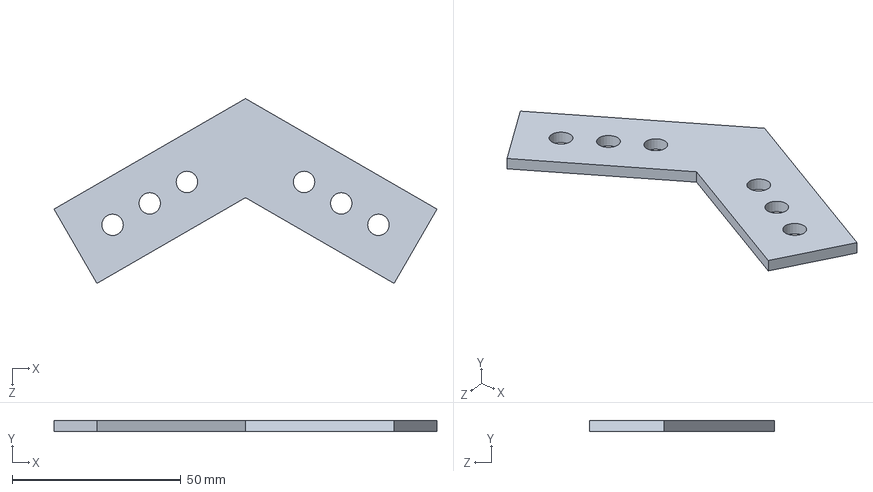
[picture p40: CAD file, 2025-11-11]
CAD Models/Bracket.SLDPRT
113.4 x 3.17 x 54.7 mm

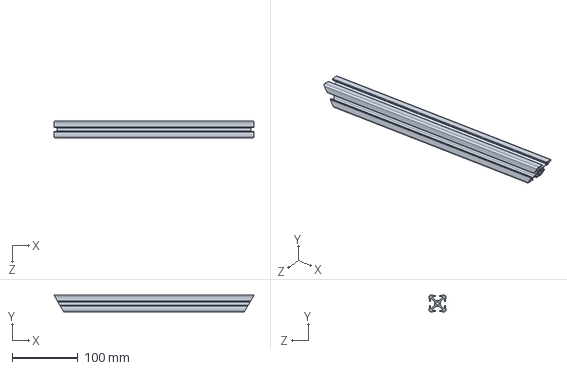
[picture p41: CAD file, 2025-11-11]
CAD Models/RailA.SLDPRT
304.8 x 25.4 x 25.4 mm

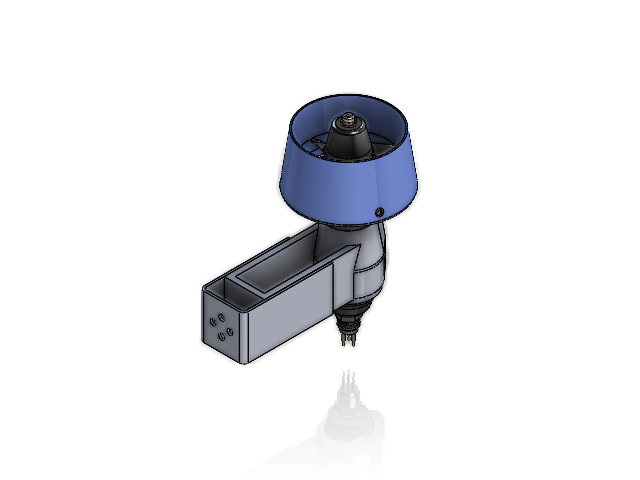
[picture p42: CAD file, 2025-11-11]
CAD Models/Thruster.SLDASM
ActuatorBracket
ThrusterClamp

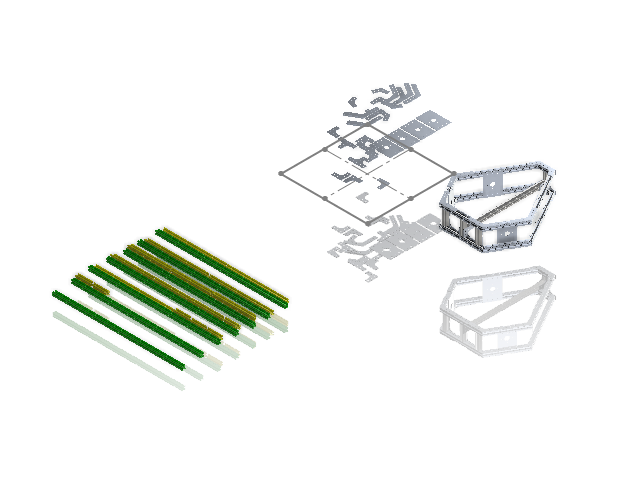
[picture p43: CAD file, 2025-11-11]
CAD Models/MaterialUtils.SLDASM
RailStock x 7
BracketBC x 8
BracketAB x 8
RailA x 6
RailB x 6
RailD x 4
RailC x 8
Bracket90 x 16
RotaryBracket x 8
RailX x 2
BracketCD x 8
RailZ x 8
BracketT x 8
StockAluminum
94444A100_Black Oxide 18-8 Stainless Steel Hex Head Screw x 2

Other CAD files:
CAD Models/OceanGigROV.SLDASM
CAD Models/ThrusterMount.SLDPRT
CAD Models/StockAluminum.SLDPRT
CAD Models/FrameSketch.SLDPRT
CAD Models/286-458.SLDPRT
CAD Models/4658N12_T-Slotted Framing Rail.SLDPRT
CAD Models/4976N35_T-Slotted Framing Fasteners.SLDPRT
CAD Models/91287A081_18-8 Stainless Steel Hex Head Screw.SLDPRT
CAD Models/91287A825_18-8 Stainless Steel Hex Head Screw.SLDPRT
CAD Models/92147A029_316 Stainless Steel Split Lock Washer.SLDPRT
CAD Models/94444A100_Black Oxide 18-8 Stainless Steel Hex Head Screw.SLDPRT
CAD Models/ActuatorBrace.SLDPRT
CAD Models/ActuatorBracket.SLDPRT
CAD Models/ActuatorMount.SLDPRT
CAD Models/Bracket90.SLDPRT
CAD Models/BracketBC.SLDPRT
CAD Models/BracketCD.SLDPRT
CAD Models/BracketT.SLDPRT
CAD Models/BracketTSmall.SLDPRT
CAD Models/Model 20WD.SLDPRT
CAD Models/RailB.SLDPRT
CAD Models/RailC.SLDPRT
CAD Models/RailD.SLDPRT
CAD Models/ScrewAssem.SLDASM

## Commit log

2025-11-11 Update README.md
    Added information about CAD models and project media folders.
2025-11-11 Update README.md
    Added details about thruster controls and clarified report descriptions.
